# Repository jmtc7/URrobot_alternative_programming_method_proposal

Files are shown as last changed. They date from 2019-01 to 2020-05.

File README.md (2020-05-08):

# Alternative programming method for UR robotic arms
This project's objective is not to create a real full-operative alternative to the current programming methods for industrial robots but to propose an idea developing a Proof of Concept to show that this approach could have potential.

The project has 2 main parts:
* **3D-printable case** to contain and protect the Raspberry Pi, a camera, a distance sensor and a fan. It also makes it possible to attach the whole system to the UR robot wirst.
* **Python scripts** to program the robot and make it able to replay the teached movements. The robot has to be running its own (simple) program to move according the Modbus TCP-received messages.

Demos of the target segmentation (color and shape filtered) and of the final results (target tracking and following and trajectory reproduction) are available in the following **YouTube videos**:

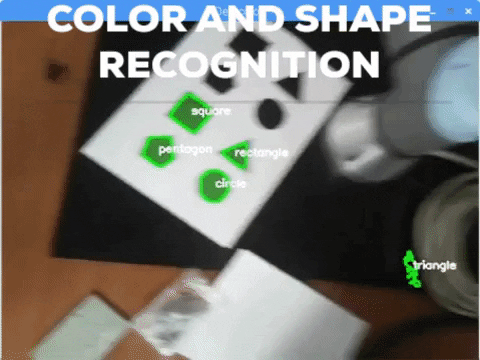
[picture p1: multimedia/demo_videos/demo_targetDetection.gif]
Target segmentation demo (https://www.youtube.com/watch?v=7s4_1wDeRGM&list=PLBYQePjTMEGEnVe6FjThMmySTzwtxLX1B&index=1)


Results demo (https://www.youtube.com/watch?v=rEhbCNIjvR4&list=PLBYQePjTMEGEnVe6FjThMmySTzwtxLX1B&index=2)

NOTE: This project was developed during my internship at [CFZ Cobots](https://cfzcobots.com/), in Elche (Spain), and submitted in a [competition](https://cfzcobots.com/i-concurso-cfz-de-aplicaciones-roboticas/) of applications designed for/with Universal Robots robotic arms.

## Documentation and usage
### Documentation
An exhaustive documentation of all the project can be found in the [project report](https://github.com/jmtc7/URrobot_alternative_programming_method_proposal/blob/master/documentation/report.pdf). A shorter version of it is in the [project presentation](https://github.com/jmtc7/URrobot_alternative_programming_method_proposal/blob/master/documentation/presentation.pdf). Even both of them are in Spanish, the next README sections are an overview of the project in English.

### Usage
In order to use this project, an Universal Robots robotic arm is needed, as well as a tool similar to the one proposed (with a camera and a distance sensor connected to a Raspberry Pi. The robot must be executing the [proposed robot program](https://github.com/jmtc7/URrobot_alternative_programming_method_proposal/tree/master/source_code/ur_program). Note that it is advisable to lower the robot velocity from the command pallete to be able to do a first test run safely. The tool must be connected to the robot so that it can write in its registers via Modbus TCP. Finally, a target will be needed, which consists in a green triangle that can be sticked in the tool which have to be followed.

Once having everything setted up as explained, the *programar.py* script should be executed in the tool. It will make the robot follow the target and store the corrections in a file named *correcciones.txt*. Once the desired trajectory is finished, the execution of this script must be stopped. Next, the robot can be moved to the desired point where we want it to start the trajectory and execute the *reproducir.py* script in the tool, which will read the corrections file and make the robot perform the programmed movements relative to the chosen start position.

## 3D case
I started attaching just the Raspberry and a camera to the wirst of the robot using flanges and adhesive tape to make some initial test and trials. I then developed a really simple 3D printed mounting that made it possible a more solid (yet **provisional**) attach between the robot and the two devices mentioned before. This mounting was composed by this two plates:
<p align="center">
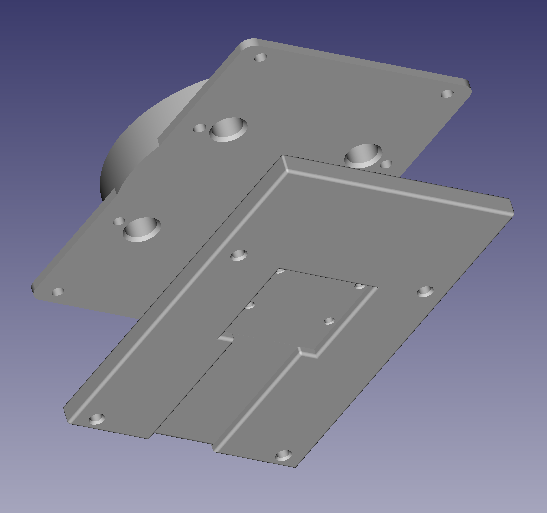
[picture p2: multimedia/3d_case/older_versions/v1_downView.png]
   
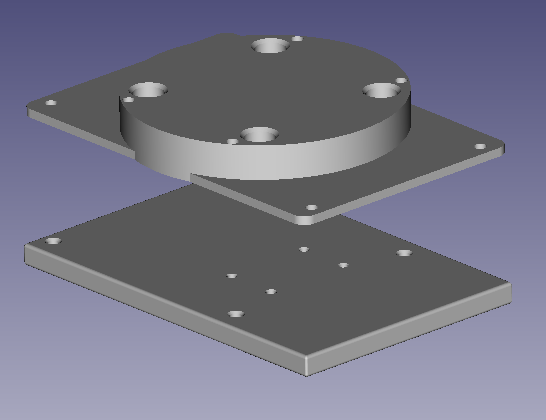
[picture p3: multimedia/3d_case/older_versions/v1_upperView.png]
  
</p>

Then, after advancing with the code, I started designing a **final version of a new case**. It will be adapted to the needs I met during the developement (such as including a distance sensor) and, obviously, will include general improvements such as a more aesthetic finish, more protection, ventilation, better and more solid coupling:
<p align="center">
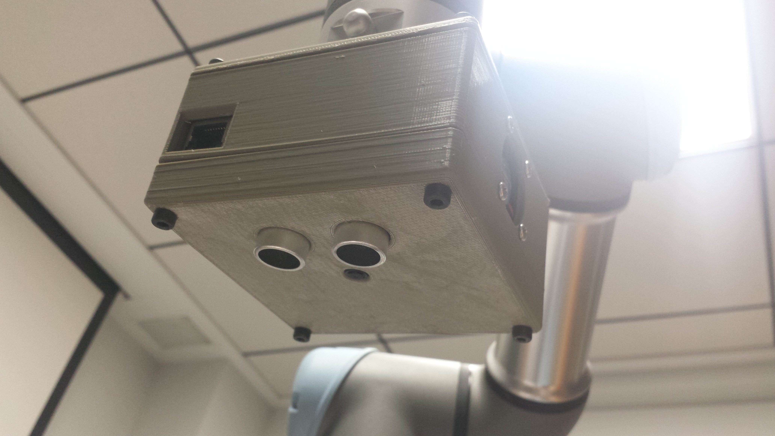
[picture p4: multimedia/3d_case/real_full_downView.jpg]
  
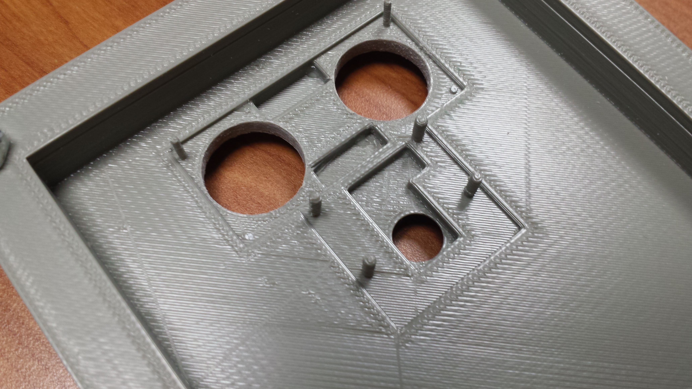
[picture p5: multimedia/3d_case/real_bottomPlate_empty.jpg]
  
</p>

<p align="center">
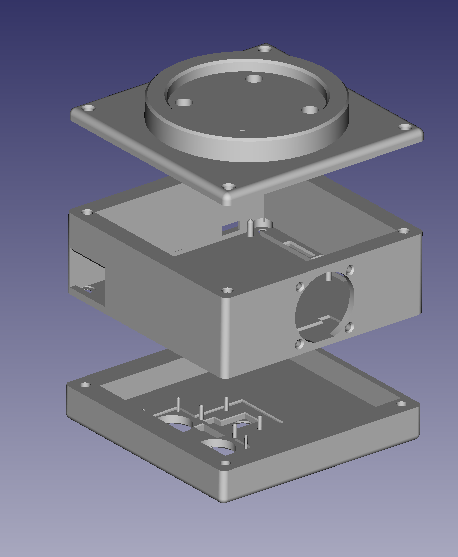
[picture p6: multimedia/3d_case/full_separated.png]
   
</p>

## Scripts
### Software in the tool
As mentioned in the introduction, in the tool, two Python scripts will be executed in the Raspberry Pi: *programar.py* and *reproducir.py*, both of them contained in the *source_code* folder.

* ***programar.py*** tracks the centroid of the biggest green triangle perceived by the camera. I convert to HSV, threshold and use the Ramer-Douglas-Peucker algorithm to classify shapes. Then, the neeeded cartesian corrections to center the centroid in the frame are calculated. Finally, they are sent to the robot (which will solve the inverse-kinematics to reach the new target) and written into a corrections file named *correcciones.txt* that will be used by the other script to reproduce the trajectory..

* ***reproducir.py***. This script does the same as *programar.py* but substituting the computer vision and corrections calculation for just reading a line of the corrections file *correcciones.txt*. The aquired data is then sent to the robot so that it will behave as it did during the programming phase.

### Software in the robot
Appart of these scripts runned on the tool, the robot has to be always processing the messages that it receive via Modbus TCP. This is done by the **7_4_pruebas_modbus** program, also contained in the *source_code* folder. This program will get the correction provided by the tool software using the robot's Modbus TCP registers and move the arm accordingly.

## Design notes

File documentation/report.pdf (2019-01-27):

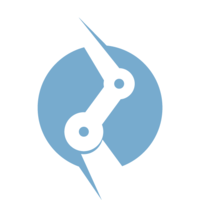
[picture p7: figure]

Prácticas extracurriculares en CFZ Cobots

Ingeniería Robótica, Universidad de Alicante

## Propuesta de un método alternativo de programación por guiado basado en visión artificial

Autor:
José Miguel Torres Cámara

Tutores:
Jorge Vergara Roa (empresa) Fernando Torres Medina (UA)

## Índice

1. Motivación, objetivos y estructura | 2
2. Resultados | 3
3. Recursos utilizados | 17
4. Otras versiones de la herramienta | 18
5. Otras opciones para el identificador | 22
6. Otras opciones para el procesado de imagen | 24
7. Otras opciones para las comunicaciones | 25
8. Análisis de resultados y conclusiones | 26
9. Trabajos futuros | 27
Referencias | 30

1

## 1. Motivación, objetivos y estructura

1.1. Programación por guiado

Actualmente se distinguen dos principales maneras de programar un robot: programación textual y programación por guiado. Mientras la textual consiste en escribir código de forma similar a como se hace en lenguajes de programación estándar, en la programación por guiado se mueve el robot hacia las posiciones que debe de alcanzar en cada momento, bien sea de forma discreta, es decir, moviendo al robot manualmente o desde la consola de programación a todos los puntos uno a uno e ir grabándolos independientemente o de forma contínua, en la que directamente se le coloca la herramienta que usará en la aplicación y se realiza la tarea que deberá reproducir el robot con la herramienta ya colocada en el extremo del mismo. Este último método es muy común en aplicaciones donde se requiere cierta habilidad o arte en la tarea, donde es complicado reproducir los movimientos que seguiría el humano artista mediante los otros métodos tradicionales. Algunas de estas tareas serían operaciones de pintura, soldadura, etc. Dada la versatilidad que supone este método así como su gran cantidad de aplicaciones y facilidad de programación de cara al usuario, durante el proyecto me centraré en él.
A pesar de todas las ventajas que supone este tipo de programación por guiado, también conlleva imprecisión en los movimientos (ya que lo mueve un humano) así como cierta incomodidad ya que el artista no estará ejecutando la tarea con su herramienta al aire, si no que tiene que arrastrar el robot tirando de ella, lo que puede suponer limitaciones espaciales así como un evidente esfuerzo extra, desenvocando en que sea prácticamente imposible realizar la tarea igual que si la herramienta no estuviese unida al robot.
A causa de esto, pensé en formas de mejorar el resultado que proporcionaba este tipo de programación tratando de evitar costes excesivos y manteniendo su sencillez de uso de cara al usuario, llegando así a la conclusión de que las opciones con más posibilidades era lograr que el robot pudiese almacenar las posiciones a seguir mientras el usuario realiza la tarea con la herramienta totalmente desacoplada del robot. De esta forma se reducirían parcialmente todos los contras comentados en el párrafo anterior.
1.2. Objetivos generales

Como principal objetivo tengo que, mis prácticas sirvan como un inicio de proyecto real, ya que en un mes no puede desarrollarse una alternativa de programación realmente práctica por lo que el objetivo, evidentemente, no es lograr una alternativa real a los métodos de programaciones actuales.
Con el objetivo de desarrollar este primer paso hacia un nuevo método de programación, pretendo desarrollar un prototipo mínimo que demuestre que es posible implementarlo, que permita descubrir posibles mejoras y que cumpla con algunas de las características que considero más importantes para este propósito, las cuales son:

2

Robustez: El prototipo debe de comportarse de forma similar en la mayor parte de los ambientes donde se ponga a prueba, tanto en un entorno controlado de laboratorio como en las muchas condiciones que puede suponer cualquier entorno industrial, ya que este último será su verdadero campo de aplicación

Efectividad: Debo lograr un seguimiento lo más cercano a la realidad que sea posible ya que, de no ser así, no tendría sentido utilizar esta propuesta. Con ese propósito, los movimientos del robot deberán ser todo lo suaves y naturales que se pueda, dando por sentado que se debe seguir la trayectoria del identificador fielmente. Otro punto importante es la velocidad con la que el robot puede seguir al objetivo sin perderlo, ya sea porque no pueda frenar de lo rápido que va o porque el objetivo vaya demasiado rápido

Sencillez: Como mencioné anteriormente, una de las principales ventajas de la programación por guiado es su carácter user-friendly, cosa que me gustaría conservar e incluso mejorar con esta aplicación. Quiero que el usuario final sólo tenga que montar el dispositivo en el robot e iniciar la ejecución del programa del robot

Comodidad: Trataré de hacer un dispositivo embebido, lo más pequeño y manejable que me sea posible

1.3. Estructura del informe

Con el propósito de lograr la mayor claridad posible en este informe, comenzaré explicando hasta donde llegué en el proyecto así como los recursos software y hardware en los que me basé para después seguir comentando otras opciones que contemplé durante su desarrollo así como algunas de las pruebas que hice para cada una de las partes del mismo. Luego analizaré los resultados y seguiré mencionando algunos de los trabajos futuros que podrían realizarse para seguir avanzando. Por último, acabaré con las conclusiones que saqué tras realizar todo el proyecto.

## 2. Resultados

Tras finalizar el periodo de prácticas logré un prototipo mínimamente funcional que era capaz de hacer que el robot siguiese al identificador (un triángulo verde), almacenar los movimientos que se hacen relativos a su posición inicial y luego repetirlos desde cualquier posición desde la que se parta (a no ser que ésta provoque la existencia de singularidades, colisiones o salidas del espacio de trabajo en algún momento de la trayectoria, es decir, limitaciones propias del robot). Todo esto lo posibilita la existencia de cuatro partes principales: una herramienta para el robot que controlada por una

3

Raspberry Pi, un programa del robot y dos programas en Python ejecutados en la Raspberry. Cada una de estas cuatro partes es la mejor versión que he podido crear de las mismas y, a continuación, paso a explicar cada una de esas versiones definitivas.

2.1. Herramienta desarrollada

Como he mencionado, he desarrollado una herramienta que puede acoplarse al extremo de cualquier modelo de los brazos robots de Universal Robots. Esta herramienta cuenta de tres partes:

Placa superior: Permite anclar la herramienta a la brida de herramienta de los brazos robóticos UR

Placa intermedia: Contiene el controlador, es decir, la Raspberry Pi (en concreto una 3B), que es la que se encarga de procesar la información captada por los sistemas de percepción y corregir la pose del robot. En esta parte de la herramienta también hay alojado un pequeño ventilador para refrigerar el sistema ya que, al estar todo encapsulado, se acumula bastante calor. También incorpora un divisor de tensión que adapta la señal que proporciona el sensor de distancia (un HC-SR04, basado en tiempo de vuelo de ultrasonidos). Evidentemente, esta placa cuenta con accesos desde el exterior al ventilador, al puerto ethernet y al microUSB de alimentación

Placa inferior: Esta última capa contiene tanto el módulo de cámara de la Raspberry (concretamente la revisión 2 del mismo) como el HC-SR04. La existencia de esta placa permite esconder tanto los cables como las PCBs del exterior, dejando únicamente visible las partes estrictamente esenciales. De este modo, logro una mayor protección para el sistema así como un acabado mucho más estético

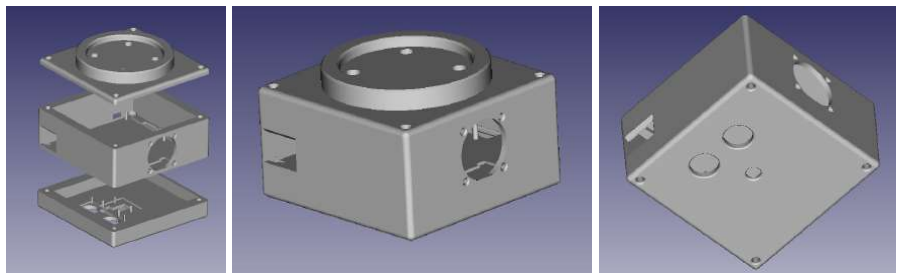
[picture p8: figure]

(a) Desglose de placas | (b) Vista superior | (c) Vista inferior

Figura 1: Diseño de la versión definitiva del soporte/herramienta

4

2.2. Script de programación (en Python) para la Raspberry

Este programa es el responsable de configurar la Raspberry tal y como se precisa en cada ejecución del programa, leer datos de la cámara y del sensor de distancia y calcular las correcciones que deben hacerse en en las posiciones X e Y del extremo del robot para reducir el error y enviárselas al robot para que se mueva, siguiendo al triángulo verde utilizado como marcador. También almacena estas correcciones en un archivo para su posterior lectura y reproducción de la tarea.

2.2.1. Dependencias y configuraciones previas

Existe una gran cantidad de recursos software que la comunidad ha creado y que facilitan enormemente el desarrollo de innumerables scripts que utilizan alguna de esas funcionalidades. Con tal de aprovechar esas bibliotecas, he utilizado algunas de ellas, como son:

time: Para contar el tiempo (función time()) que pasa entre que se emite la señal con el sensor de distancia hasta cuando se recibe y para hacer pausas (función sleep()) en varias partes del código

cv2 (OpenCV): Para capturar frames del módulo de cámara así como para realizar todo el procesado de imagen

pymodbus.client.sync: Para escribir los cuatro registros Modbus del servidor que se ejecuta sobre el armario de control del robot. Utilizo esos cuatro registros para indicar las correcciones que deben hacerse en la posición del extremo del robot para que este siga estando sobre el triángulo verde

os.path: La necesito para utilizar la función isfile(), que me permite comprobar si en el directorio actual ya existe un archivo con correcciones almacenadas de otro proceso de programación previo. En caso de detectar que ya existe un archivo, se le comunica al usuario y se da la opción de abortar la ejecución o de continuar y sobreescribirlo

RPi.GPIO: Me permite utilizar los pines GPIO (General Purpose Input/Output) para tomar lecturas del sensor de distancia

Por lo referente a la secuencia de inicialización del programa, comienzo inicializando algunas constantes de configuración, como son la dirección IP del robot y el puerto donde este tiene abierto el servidor Modbus-TCP o como la distancia aproximada (en Z) entre el sensor de distancia y la cámara, que empíricamente determiné que rondaba los 6 milímetros. Otra constante de mucha importancia es la longitud que tendrá el filtro de media móvil (LONG FILTRO) que utilizo. Por defecto está establecida a 4. Elevarla supondrá más estabilidad y robustez pero menos velocidad y precisión. También se establece un intervalo (AREA LOW y AREA MAX) en el que debe estar el area del triángulo verde (identificador) percibido por la cámara. Por último, también se

5

permite configurar el tamaño de la ZONA TOLERANCIA. Esta constante es el número por el que se dividirá el tamaño del frame captado, creando un rectángulo en el centro del mismo con las dimensiones que resulten de esas divisiones. Cuando el centro del identificador esté en ese rectángulo, se considerará que el robot está sobre el triángulo a seguir, por lo que no se moverá. Esto quiere decir que disminuir el tamaño del rectángulo (es decir, aumentar el valor de esta constante) supondrá más precisión pero aumentarlo demasiado hará que el rectángulo sea muy pequeño, pudiendo hacer que no se logre posicionar el centro del identificador en el mismo, haciendo que el robot oscile en torno a la posición sobre la que debería mantenerse estático.
Tras definir algunas funciones auxiliares (que explico en la siguiente sub-sub-sección del informe), continúo con otras inicializaciones que NO deben ser modificadas. La primera de estas es la del sistema de visión, es decir, lograr acceder al módulo de la cámara y leer un frame con éxito. En caso de no conseguirlo, se le indicará al usuario y el programa finalizará automáticamente. Se continúa con el sensor de distancia, inicialización para la que deshabilito las advertencias de posibles fallos que se hayan cometido en otros programas que usasen los GPIO y no los reconfigurasen debidamente. También indico que utilizaré la numeración de la placa y especifico los pines a los que se conectarán los pines Trig (disparador) y Echo (receptor) del sensor, además de configurarlos como salida y como entrada, respectivamente.
Tras configurar los sistemas de percepción, continúo con las comunicaciones, es decir, abriendo el socket que me permite escribir los registros del servidor Modbus del robot. En caso de que sucediese algún error durante la conexión, se informará al usuario y se finalizará la ejecución de forma automática. Tras esto, abro el archivo de escritura, que estará en el mismo directorio que el programa y se llamará çorrecciones.txt”. Comienzo comprobando si ya existe un archivo con ese nombre en el directorio. En caso positivo se informará al usuario y se dará la opción tanto de abortar la ejecución como de continuarla (y sobreescribir el archivo).
Continúo las inicializaciones declarando algunas variables para el procesado de imagen, tales como el intervalo en HSV que se considerará verde, que determiné empíricamente por mi cuenta. También leo las dimensiones de los frames y asigno valores iniciales a algunas variables por cuestiones de optimización de código como evitar declaraciones y destrucciones iterativas que consuman tiempo y coste computacional innecesariamente. Por último, adapto algunas variables del algoritmo al entorno según la distancia que haya entre la superfície más próxima a la cámara y la cámara, ya que de esta magnitud dependerán el tamaño de las correcciones que se le ordenen al robot. Tras inicializar algunas variables por los mismos motivos que en la inicialización del procesado de imagen, tomo varias medidas del sensor de distancia (el doble de elementos contenidos en el filtro de media móvil), de las cuales hago la media, considerando al resultado de la misma la distancia cámara-superficie anteriormente mencionada tras añadirle la corrección de la constante de configuración. Por último, calculo los desplazamientos máximos que debería hacer el robot en X e Y para seguir al identificador. Estas correcciones será la distancia real que hay entre lo que en el frame aparece en el centro del mismo y en la mitad de los bordes derecho o izquierdo (corrección en X) y en la mitad de los bordes

6

superior o inferior (corrección en Y). La relación entre la altura y esas distancias las obtuve con cálculos trigonométricos sencillos que no incluí en el códiogo por aligerarlo. Estos cálculos utilizan los ángulos de visión de la cámara y la ley del seno.
Sabiendo que, según [1], el ángulo de visión de la cámara es de 62.2◦ en X y de 48.8◦ en Y, es posible calcular las correcciones de la siguiente manera:

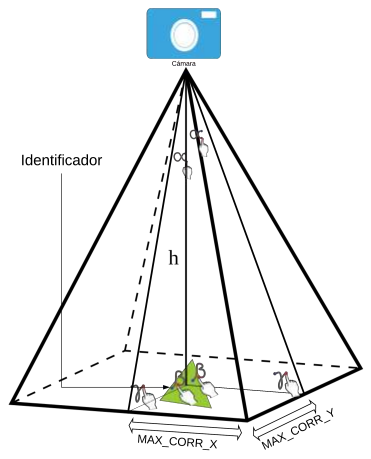
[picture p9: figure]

Figura 2: Representación del área de visión de la cámara

Cálculo de la corrección máxima en X
Angulo de visión en X = 62.2 ´ | ◦
α =

62,2
2 = 31.1◦
h = lectura del sensor de distancia β = 90◦
γ = 180 − 90 − 31,1 = 180 − 121,1 = 58.9◦
Teorema del seno:

CORR MAX X
sen(α) | = h sen(γ)

CORR MAX X =h · sen(α)
sen(γ)

=

=

h · sen(31,1)
sen(58,9) = 0.6032386 · h

Cálculo de la corrección máxima en Y
Angulo de visión en Y = 48.8 ´ | ◦
α =

48,8
2 = 24.4◦
h = lectura del sensor de distancia β = 90◦
γ = 180 − 90 − 24,4 = 180 − 114,4 = 65.6◦
Teorema del seno:

CORR MAX Y
sen(α) | = h sen(γ)

CORR MAX Y =h · sen(α)
sen(γ)

=

=

h · sen(24,4)
sen(65,6) = 0.4507694 · h

7

2.2.2. Funciones auxiliares

En pos de un código lo más limpio y claro posible, he definido varias funciones auxiliares que me permiten evitar la inclusión en el cuerpo principal del programa de código que dificultarían su lectura. Estas funciones son:

media movil(): Me permite añadir robustez y estabilidad a las lecturas de posiciones de la característica en el frame actual. Recibe como argumentos de entrada dos vectores que almacenan el historial de las últimas posiciones (en píxeles) del identificador. Uno de los historiales es sólo de las coordenadas X y, el otro, de las Y. Los historiales albergarán tantas medidas como indique la constante de configuración LONG FILTRO. Cuanto más alto sea su valor, más robusto será el proceso a lecturas erróneas (ruido puntual) pero se seguirá a la característica con menor precisión y velocidad. Un valor aconsejable es 4. A partir de los dos historiales, calcula la media y devuelve los resultados

detectarTriangulo(): Evalúa si un contorno es o no un triángulo. Basada en el algoritmo de Ramer-Douglas-Peucker, que simplifica un segmento curvo aproximando varios segmentos lineales. Esto permite saber cuántos vértices principales se tienen en un contorno determinado. El contorno a analizar es su único argumento de entrada. Este contorno estará formado por una serie de puntos obtenidos tras el procesado de la imagen. Simplemente realizo la aproximación por segmentos lineales y, en caso de haberse aproximado con tres segmentos, confirmo que la forma es un triángulo devolviendo un valor True. En caso de que la aproximación no resultase en tres contornos, se devuelve False

medirDistancia(): Hace uso de los pines GPIO para medir la distancia desde el sensor de distancia (y de la cámara) hasta el objeto más cercano (superfície donde esté el identificador). Pone a nivel bajo el pin que ordena que se emitan señales desde el sensor y se hace una pequeña pausa (2 microsegundos) para que de tiempo a que se haya apagado. Después, se enciende dicho pin, ordenando una emisión de ultrasonidos para continuar con otra pausa (de 10 µs) para asegurar la emisión antes de volverlo a apagar. Después se comienza a contar tiempo cuando se recibe un valor alto a través del pin que indica si el receptor recibe o no. La cuenta se detiene cuando para de recibir. Por último, se calcula el tiempo transcurrido entre estos dos eventos y se utiliza ese dato para calcular la distancia hasta el objeto más próximo en metros. El resultado de esta conversión será el valor que devuelva la función

2.2.3. Bucle principal: Procesado de imagen

El objetivo del procesado de imagen que realiza mi programa es obtener el centroide del contorno (sucesión de puntos) del triángulo verde más grande que aparezca en el frame. Con este propósito, desarrollé un procesado de imágen divisible en dos partes: discriminación por color y por forma y tamaño.

8

La discriminación por color fue por la que empecé, detectando el verde, ya que tras numerosas pruebas, determiné que era el color que se reconocía con más robustez antes cambios de iluminación y para áreas de distintos tamaños y formas. Para esta parte, comienzo pasando de RGB a HSV, ya que en este espacio de color se separa el tono de la luminosidad, logrando muchísima más robustez frente a variaciones en la luminosidad. Además, dada su distribución cilíndrica de los colores, es más sencillo establecer un único intervalo en el que se localizan los colores deseados. Esta transformación la realizo con la función cvtColor() de OpenCV[3].
Una vez convertida la imagen a HSV, creo una imagen binaria en la que los píxeles cuyo valor entren en el intervalo establecido en las constantes de configuración aparecerán en blano y, el resto, en negro. La ubralización la permite el método inRange().

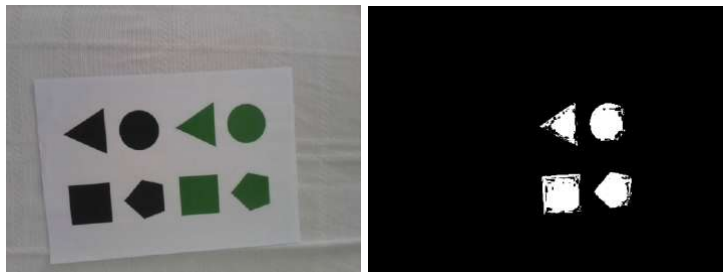
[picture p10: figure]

(a) Frame original | (b) Frame binarizado

Figura 3: Umbralización por color

Sobre esta imagen binaria, con findContours(), también de OpenCV[3], obtengo todos los contornos que envuelven a las figuras que en ella aparecen, que incluirán tanto las áreas verdes que aparezcan como los ruidos que figuren en la imagen por cualquier causa.
Una vez obtenidos todos los contornos, paso a discriminarlos por tamaño y forma. Se recorre el vector de contornos obtenido (la variable cnt) para evaluar el área que encierra cada uno de ellos, siendo esta la primera ”barrera”que deben pasar para ser considerados el identificador. Si el contorno que se esté evaluando es el mayor hasta el momento, se comprueba si además es un triángulo (con mi función detectarTriangulo()). En caso de cumplir ambas condiciones, se almacena tanto el contorno como el área que encierra para poder disponer de los mismos después.

9

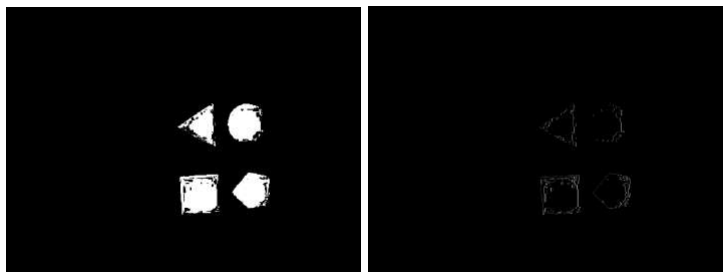
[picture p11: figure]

(a) Frame binarizado | (b) Contornos extraidos

Figura 4: Extracción de contornos

Tras analizar todos los contornos detectados, se dispondrá del que corresponda al triángulo verde más grande de la imagen, habiendo discriminado tanto triángulos de otros colores como ruidos pequeños, posibles reflejos, otras formas verdes, etc.

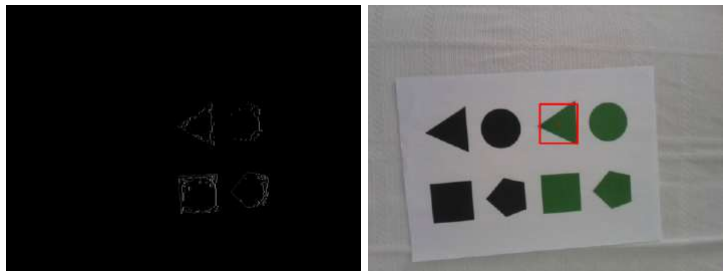
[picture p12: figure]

(a) Contornos extraidos | (b) Detección definitiva

Figura 5: Discriminación por forma

El hecho de haber escogido al triángulo como forma discriminadora vino dado tras un análisis con varias formas (triángulos, cuadrados, rectángulos, pentágonos y círculos) de varios colores y tamaños. Traté de detectarlos desde distintas distancias y orientaciones y el que se comportaba mejor casi siempre era el triángulo. Las figuras con más aristas se confundían cuando las enfocaba con inclinaciones elevadas o desde distancias relativamente largas.

10

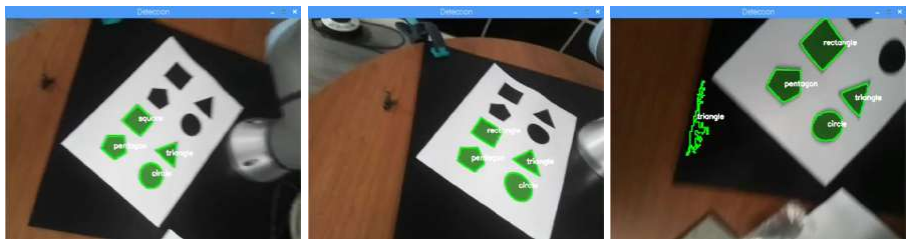
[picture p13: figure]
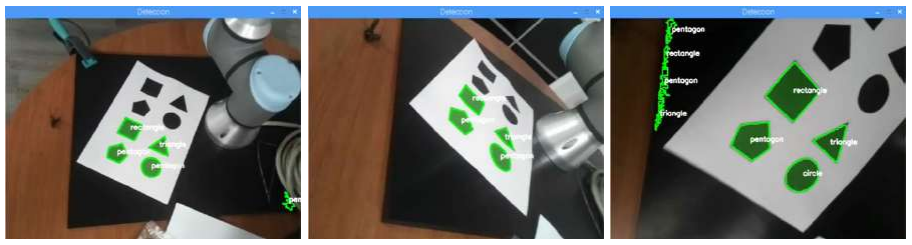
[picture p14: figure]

Figura 6: Detección y clasificación de varias formas con varios ángulos y tamaños

Tal y como se aprecia en las imágenes (extraídas de un vídeo en el que detectaba y clasificaba formas on-line), el círculo es el que más se confunde, normalmente con figuras de muchos lados (considero que es un círculo cuando se detectan 6 o más vértices). Sin embargo, en ningún momento se confunde al círculo con un triángulo. Dado que, como he mencionado, las imágenes son de un vídeo, algunos frames eran muy borrosos, por lo que no he incluido uno de ellos en el que el pentágono se confunde con un círculo. Estos dos hechos dejan como mejores opciones a los cuadrados/rectángulos y a los triángulos. Dado que, como he mencionado, el círculo nunca se ha confundido con un triángulo pero sí con un cuadrado, opté por descartar a los cuadriláteros, ya que podría darse el caso en el que hubiese un círculo verde en la escena y este deba ser discriminado, cosa que se logra utilizando triángulos en lugar de cuadrados o rectángulos. También se observa que los ruidos son formas pequeñas, por lo que se discriminarán, así como que otras formas de otros colores, como negras, no son tenidas en cuenta.
La última discriminación consiste en comprobar si el área del contorno resultante está en el intervalo definido en las constantes de configuración(AREA TOP y AREA LOW). Esto permite detectar cuándo ningún contorno cumplía con todos los requisitos (area max seguirá siendo 0, estando por debajo de AREA LOW) así como detectar posibles errores en los que se considere un contorno exageradamente grande. Si el contorno está en el intervalo definido, calculo su centroide ([cx, cy]) utilizando los momentos del mismo.
En caso de que no haya ningún contorno triangular que encierre un área de un tamaño aceptable, se notifica y se centra toda la potencia de procesado en encontrarlo, haciendo un continúe, obligando a reiniciar el bucle (que vuelve a

11 tomar otro frame y a procesarlo) en lugar de seguir con el cálculo y el procesado de las correcciones.

2.2.4. Bucle principal: Cálculo de correcciones

Tras el procesado, he obtenido los valores de cx y de cy, por lo que ya se puede continuar con el siguiente paso: transformar la posición del identificador en la imagen en correcciones para la posición del extremo del robot.
Antes de calcular nada, se guardan las coordenadas en píxeles del identificador en los historiales historial x e historial y y se comprueba su longitud. En caso de ser menor que la configurada en la constante LONG FILTRO, se vuelve a iniciar todo el procesado de imagen para tomar otra medida de la posición del identificador, de forma que hasta no haber llenado un ”buffer”del filtro, no se inicia el funcionamiento normal del bucle.
En caso de que se disponga de suficientes medidas, se elimina la más antigua (el elemento 0 de los historiales) y se calcula la media, considerando el resultado de la misma la posición actual del identificador, siendo esta la que se utiliza para calcular las correcciones.
Las correcciones en cada eje (X e Y) se calcularán sólo si en ese eje el identificador está fuera de la zona de tolerancia (rectángulo verde de la figura 6), es decir, fuera del rectángulo que se establece en el centro del frame en el que se considera que, si el centro del identificador (punto rojo de la figura 6) está dentro, el robot está sobre el mismo, caso en el que a la corrección en ese eje tomará un valor de
0. El uso de esta zona viene dado porque, si no la utilizaba o si era demasiado pequeña, el robot oscilaba sobre la posición objetivo. En la siguiente imagen es una catorceava parte del temaño total del frame:

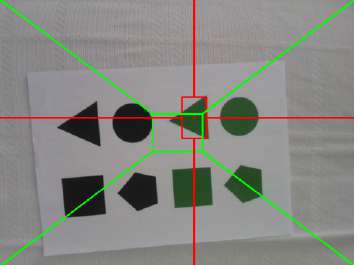
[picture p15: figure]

Figura 7: Zona de tolerancia

En caso de ser necesaria corrección en alguno de los ejes, calculo y normalizo (entre 0 y 1) el error de la posición del centro del identificador, asumiendo como posición deseada el píxel central del frame. A ese valor entre 0 y 1 lo multiplico por la corrección máxima calculada en el eje que corresponda (DESPLAZAMIEN-TO MAX X para el eje X y DESPLAZAMIENTO MAX Y para el eje Y), obteniendo

12 el desplazamiento que el robot deberá hacer para posicionar la cámara (que gracias al diseño de mi herramienta, tiene el eje Z alineado con la muñeca del robot) sobre el identificador.

2.2.5. Bucle principal: Procesado de correcciones

Tras haber calculado las correcciones a hacer (correccionX y correccionY ), paso a procesarlas. Este procesado consiste únicamente en comunicárselas al robot por Modbus-TCP y en anotarlas en el archivo correcciones.txt.
Para comunicarle los resultados al robot utilizo cuatro registros Modbus. El uso de cuatro registros en lugar de dos es porque estos sólo pueden contener valores positivos, así que escribo las correcciones a hacer en X y en Y en los registros 128 y 129 y sus signos en los 130 y 131, escribiendo ”1”si es positivo y ”0”si es negativo. Por lo referente a los registros 128 y 129, escribo el valor absoluto del resultado de dividir las correcciones multiplicadas por 1000 y divididas por 2. Las divido entre 2 para evitar sobreoscilación durante el seguimiento, sacrificando velocidad. El hecho de multiplicar las correcciones por 1000 es debido a que los registros sólo pueden contener números enteros, por lo que lo escribo en milímetros en lugar de metros cosa que luego, en el programa del robot, tengo en cuenta.
Por último, también escribo las correcciones en el archivo. Para no perder tiempo, no vuelvo a hacer las operaciones de multiplicar por 1000 y dividir entre 2, cosa que SÍ que hago en el programa de reproducción, ya que este conlleva una carga computacional mucho menor.
2.2.6. Proceso de finalización

Con tal de lograr una finalización lo más limpia posible, he tratado de contemplar todas las posibles excepciones, tales como errores en las diferentes inicializaciones, peticiones del usuario o una interrupción de teclado (Ctrl + C). Si ocurre cualquiera de estas cosas, libero la cámara (liberando el archivo de captura así como la memoria reservada para su uso), cierro el socket que utilizo para Modbus/TCP (sólo si se ha conseguido abrir durante las inicializaciones), libero el archivo de escritura y reseteo los GPIO utilizados durante el programa (11 y 13 según la numeración de la placa para el sensor de distancia).

13

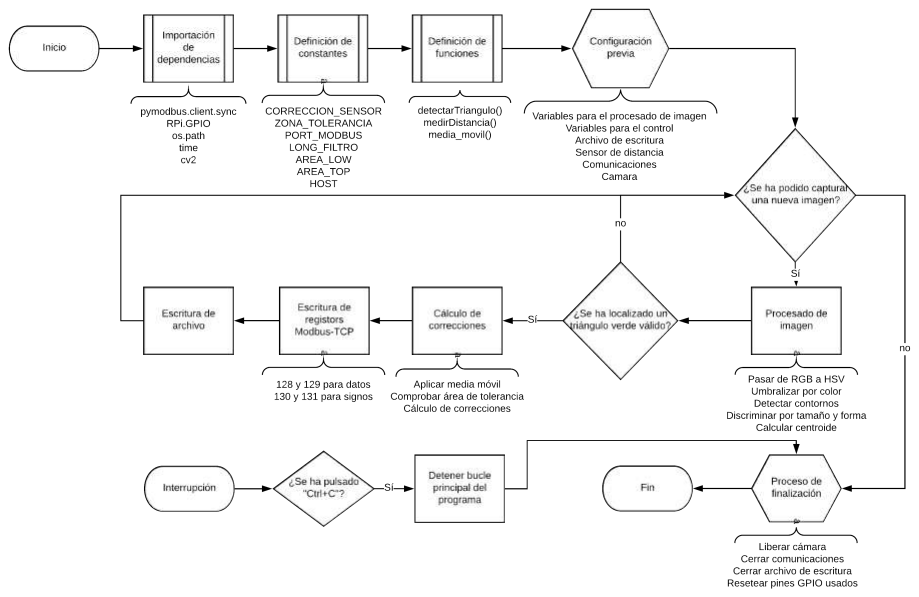
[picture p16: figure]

Figura 8: Diagrama de flujo de programar.py

2.3. Script de reproducción (en Python) para la Raspberry

Este programa se ejecutará una vez se haya programado al robot mediante una ejecución completa, exitosa y sin errores del anterior programa (caso normal), de forma que se haya creado el archivo. Este script permite que se reproduzcan los movimientos realizados durante la programación sin perder el tiempo que se perdió con el procesado de imagen y cálculo de correcciones, además de consumir menos recursos, ya que exige mucha menos memoria y potencia de cálculo para su ejecución.
Dado este método de reproducción, no hace falta cargar un programa distinto en el robot, ya que basa las comunicaciones en el mismo funcionamiento del programa anterior, escribiendo los mismos 4 registros Modbus.
2.3.1. Dependencias y configuraciones previas

Al igual que en el caso del programa anterior, utilizo algunas librerías ya desarrolladas por la comunidad. Aunque menos que en el caso anterior, todas también se usan en el

14 otro programa. Las dependencias que importo son os, time y pymodbus.Client.sync. Les doy los mismos usos que en el script para programar al robot.
Además de incluir estas dependencias, antes de iniciar el funcionamiento normal del programa, realizo una serie de configuraciones previas, como son la declaración de las constantes de configuración, como la IP del robot (HOST), el puerto donde el mismo tiene el servidor Modbus (PORT) y el tiempo que se deja entre cada escritura de registros (DELAY ITERACIONES). Este tiempo está configurado a 0.048496 s porque es el tiempo medio que se tardaba en una iteración completa del bucle del script de programación. De este modo, el comportamiento durante al reproducción será lo más similar posible al que tuvo lugar durante la programación.
A continuación, al igual que hacía en el otro programa, abro el archivo de lectura donde se almacenaron las correcciones realizadas durante la programación y abro un socket para comunicarme por Modbus-TCP con el robot. Tras este último paso, escribo un 0 en los registros de correcciones del robot para que, en caso de que por cualquier motivo, tuviesen otro valor, el robot no se moviese cuando no debe hacerlo. También tengo en cuenta posibles errores, como que el archivo no exista o que haya algún fallo durante la conexión con el servidor, en cuyo caso, se le comunicaría al usuario y se abortaría la ejecución del programa.
2.3.2. Bucle principal

Este programa únicamente lee las correcciones almacenadas en el archivo, las transforma de tipo y las escribe en los registros Modbus por Modbus-TCP que usaba la otra aplicación, permitiendo que el robot las lea y corrija su posición. Entre escritura y escritura se realiza un pequeño delay que simula el tiempo que se tardó en todo el procesado de imagen y cálculo de correcciones en el otro programa, reproduciendo todo lo fielmente posible los movimientos realizados.
El usuario podrá regular la velocidad de reproducción de movimientos desde la barra de velocidad de la consola de programación y, como opción excepcional, reduciendo el tiempo de delay, aunque la diferencia será mínima.
2.3.3. Proceso de finalización

Para finalizar este programa, repito una parte de la secuencia de finalización del otro programa. Concretamente, la de cerrar el socket y liberar el fichero desde el que se leen las correcciones almacenadas.

15

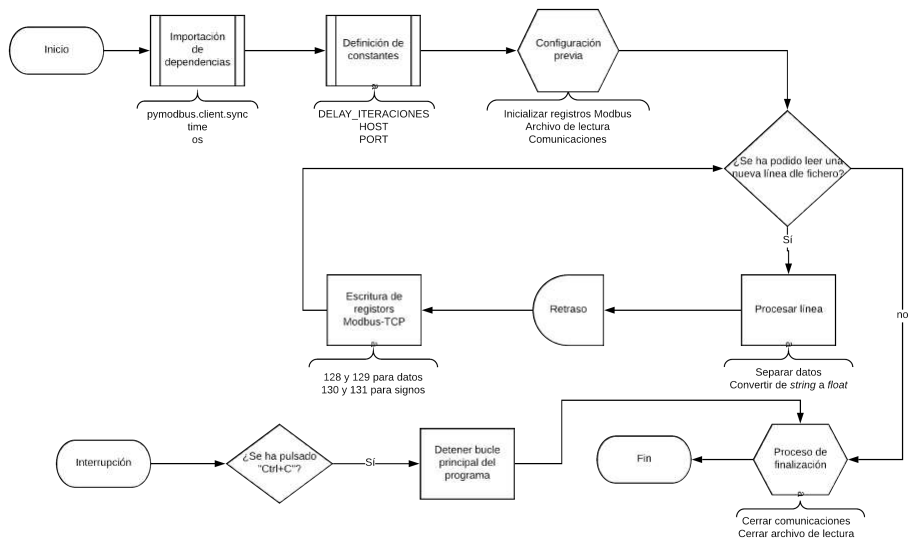
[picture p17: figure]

Figura 9: Diagrama de flujo de reproducir.py

2.4. Programa del robot

Para llevar a cabo las correcciones calculadas por la Raspberry, desarrollé un pequeño programa para el robot que procesaba los datos enviados a través de Modbus-TCP al robot y hacía uso de algunas de las funciones que los UR ponen a disposición de los desarrolladores, como get actual tcp pose(), read port register(), pose trans() o MoveL(). Este programa es tremendamente sencillo pero permitía ahorrarle a la Raspberry una considerable carga computacional y simplificar muchísimo los códigos, cosa que era uno de mis principales objetivos, ya que el cuello de botella reside ahí, ya que se tarda sobre 50ms en llevar a cabo una iteración del bucle de control mientras que el robot es capaz de actuar recibiendo órdenes a 125Hz (una cada 8ms). Es debido a este ahorro temporal por lo que decidí utilizar este programa, ya que también disponía de otras versiones en las que no era necesario ejecutar absolutamente nada desde el robot. Además, al obligar a que cada programa se ejecute con una configuración de instalación concreta, permite reducir la posibilidad de que el usuario final tenga problemas que le puedan resultar complicados de solucionar, como algunos relacionados con la configuración de la red local RPi - robot.
El programa simplemente lee los registros Modbus de correcciones escritos por el programa de la Raspberry y, en caso de ser distintos de 0 (para no perder tiempo

16 inútilmente), les asigna el signo que les corresponda leyendo el otro par de registros Modbus, transforma la posición actual del TCP en la deseada y ordena un movimiento lineal hasta la misma, reduciendo el error en la medida que la Raspberry lo ordene.

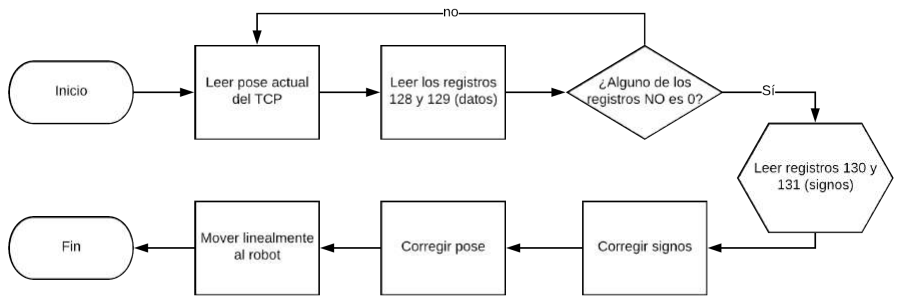
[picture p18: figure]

Figura 10: Diagrama de flujo del programa del robot

## 3. Recursos utilizados

3.1. Dispositivos involucrados

Como ya he mencionado, el elemento central de todas las pruebas que he realizado, ha sido una Raspberry Pi (modelo 3B concretamente). Este ordenador lo manejaba a través de una conexión VNC desde mi portátil. El otro factor constante en mis experimentos era un robot UR3 de la serie CB de Universal Robts.
Por otro lado, he ido utilizando varios accesorios para las pruebas, como la versión 2.1 de la cámara de la Raspberry, un módulo HC-SR04 para medir distancias, una IMU MPU6050 y, para algunas pruebas, un Arduino UNO.
3.2. Recursos software

Dejando de lado el Polyscope ejecutado sobre el Debian del UR3, he estado utilizando Raspbian corriendo sobre la RPi. Así mismo, para realizar pruebas de cada programa utilizaba Python y luego transcribía el código definitivo a C++, para poder compilarlo y obtener un binario que pudiese ejecutarse más rápido de lo que un script interpretado por el intérprete de Python podría. Sin embargo, dejé las versiones finales

17 en Python porque consideré que se alcanzaban velocidades aceptables, además de la inmensa diferencia a la hora de leer y depurar el código, siendo en el caso de Python mucho más sencillo.
Respecto a recursos más relacionados con mi aplicación y pruebas, he utilizado la librería Armadillo para C++ para implementar parte de los códigos con una carga matemática más compleja (como cálculo pseudoinversas, etc.). También usé OpenCV para llevar toda la parte de visión, tanto en C++ como en Python. Por lo referente a las comunicaciones, usé los paquetes socket y pymodbus en Python (para TCP y Modbus respectivamente) así como algunos otros de uso común como time, numpy, struct , os o RPI.GPIO.
Por otra parte, para testear las comunicaciones utilicé la versión 3 de socketTest, un programa que permitía a la máquina que lo ejecutase ser cliente o servidor TCP en la IP y puerto que se le configurase. Para Modbus hice uso de diagslave, que actúa como servidor. Ambos están disponibles tanto para Windows como para GNU/Linux.

## 4. Otras versiones de la herramienta

Para realizar pruebas era necesario tener la cámara en el extremo del robot de forma que la cámara viajase con el mismo, ahorrando el máximo de transformaciones entre sistemas de coordenadas o conversiones de desplazamientos innecesarias. En un inicio utilicé simplemente cinta adhesiva, aunque para las primeras pruebas fijé la Raspberry al robot con bridas y limité el uso de la cinta para sujetar la cámara al extremo del robot:

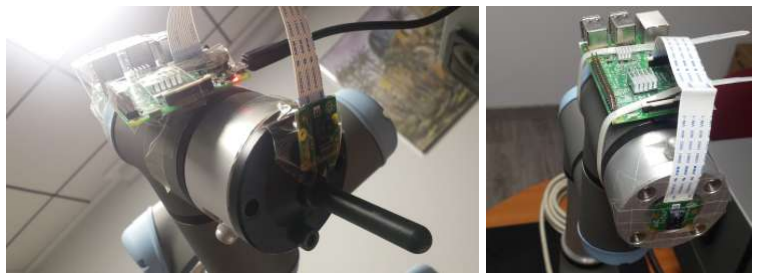
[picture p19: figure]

(a) Sujeción con cinta adhesiva | (b) Sujeción con bridas

Figura 11: Sujeciones provisionales

Sin embargo, como es evidente, esta no fue la sujeción final. Tras numerosos bocetos, diseñé varias posibles herramientas para el robot que permitiesen la máxima

18 limpieza y practicidad posibles. Para diseñar las piezas de las herramientas utilicé FreeCAD[6] y para las impresiones 3D, una RAISE 3D con ABS gris.

4.1. Primera versión de la herramienta

El principal problema que tenía es que, cuando fallaba el control, dadas las limitaciones físicas que suponía la longitud del cable de la cámara, muchas veces se desconectaba y en ocasiones me tocaba reinicar la Raspberry porque no la detectaba tras reconectarla, etc. Esto suponía una gran pérdida de tiempo además de ser intolerable para cualquier aplicación real. Por esto, decidí optar por un soporte que uniese la Raspberry y la cámara haciendo que ambos dispositivos se muevan con la tercera muñeca del robot.
Varios de mis diseños establecían el riesgo de que la Raspberry se chocase con alguno de los últimos eslabones con relativa facilidad ante movimientos inesperados del robot. Sin embargo, acabé optando por, a pesar de que el resultado sería más voluminoso, dejar paralelas tanto la Raspberry como la cámara al muñón del robot utilizando dos placas, una de las cuales iría enganchada al extremo del robot por encima y a la Raspberry y a la segunda placa por debajo. La cámara se atornilla por la parte inferior de la segunda placa.

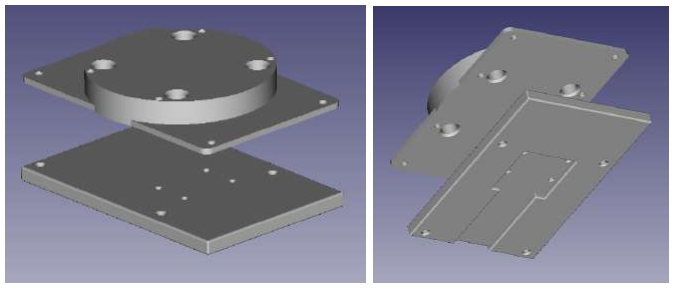
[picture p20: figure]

(a) Vista superior ideal | (b) Vista inferior ideal

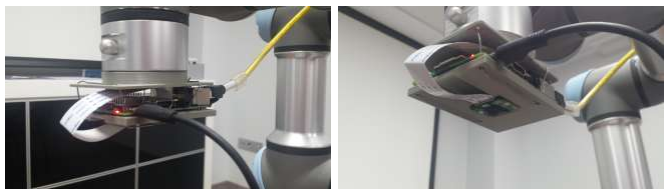
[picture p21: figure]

(c) Vista superior real | (d) Vista inferior real

Figura 12: Diseño de la primera versión del soporte/herramienta

En este soporte el principal problema que tuve fue encontrar los tornillos

19 y pilaretes necesarios como para que quedase bien anclado todo, ya que debían ser relativamente largos dada la magnitud de los agujeros, que estaba limitada por los anclajes de la Raspberry y de la cámara. Así mismo, el hardware quedaba bastante desprotegido y no es estético ver todos los cables y componentes al aire.

4.2. Segunda versión de la herramienta

En una segunda versión, a pesar de que la anterior era funcional, me enfoqué en hacer un soporte más estético, además de añadir ciertas mejoras, como la presencia de un hueco para un pequeño ventilador que refrigere el sistema y otro para añadir el sensor HC-SR04 para medir distancias. Además, todo quedaba completamente cubierto, pasando a mejorar los apartados estéticos y de protección respecto a la versión anterior.
Esta segunda versión sólo deja al descubierto las partes esenciales, tales como los agujeros para anclar la herramienta al robot, los agujeros para los tornillos que unen cada una de las tres placas y los agujeros para poder acceder al puerto ethernet, al microUSB de alimentación, al objetivo de la cámara y al emisor y el receptor del sensor de distancia.

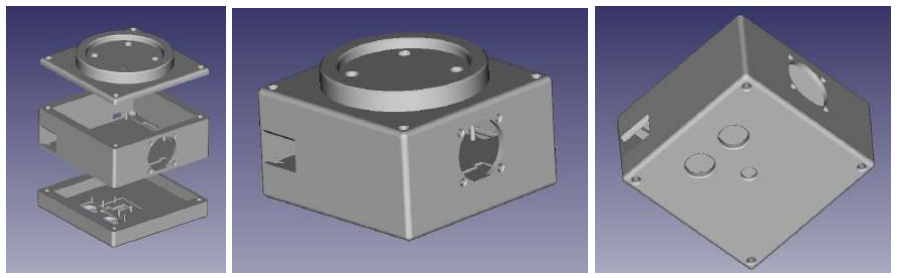
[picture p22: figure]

(a) Desglose de placas | (b) Vista superior ideal | (c) Vista inferior ideal

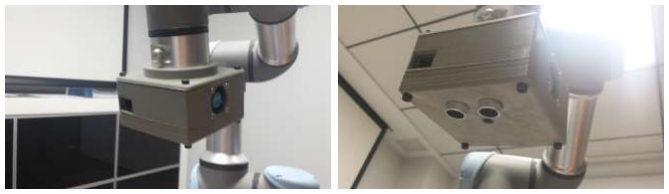
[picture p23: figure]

(d) Vista superior real | (e) Vista inferior real

Figura 13: Diseño de la segunda versión (y definitiva) del soporte/herramienta

La placa inferior tiene particular complejidad debido a los surcos que permiten colocar la cámara y el sensor de forma que queden bien sujetos aprovechando las

20 características físicas de los mismos. Todo esto se aprecia en más detalle en las siguientes imágenes:

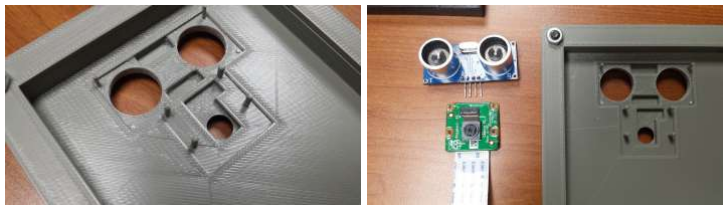
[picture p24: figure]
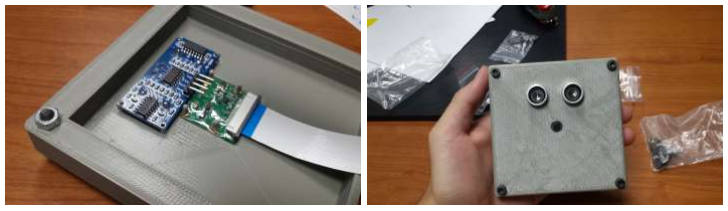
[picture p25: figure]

Figura 14: Vistas detallada de la placa inferior

A continuación muestro parte del proceso de diseño de esta herramienta, como el primer boceto a mano alzada sobre el papel y algunos recortes que realicé para pulir detalles y comprobar que las medidas eran las adecuadas:

21

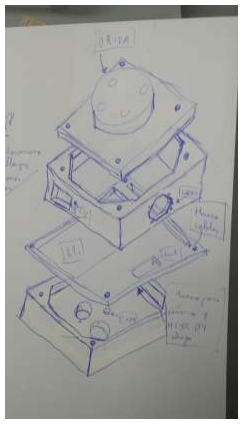
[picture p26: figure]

(a) Boceto inicial

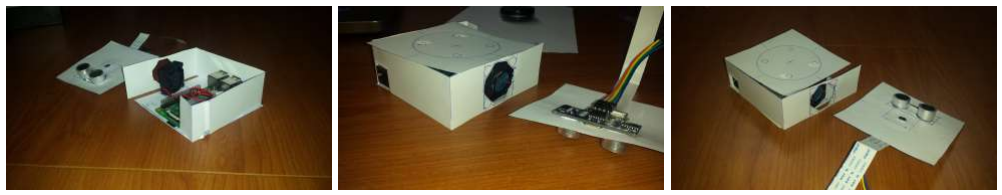
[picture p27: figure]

Figura 15: Boceto y construcciones en papel de la segunda versión

## 5. Otras opciones para el identificador

Enfocando el proyecto desde la opción del control visual, todas las opciones para detectar la herramienta que mejor resultado me dieron (midiendo la calidad según la velocidad y robustez con las que obtenía los resultados) se basaban en segmentación y, las finales, también en detección por formas (más robustez a cambios de iluminación, reflejos y ruido aunque con más carga computacional). Hasta que llegué al triángulo verde, realicé pruebas con varios patrones:

Cuatro puntos negros sobre fondo blanco (y puntos blancos sobre fondo negro). Logrando un alto contraste que favorecía la sencillez de la detección y permite una segmentación en intensidad RGB, disminuyendo bastante la carga computacional pero arriesgando la robustez, ya que pueden detectarse falsos positivos con gran facilidad en entornos no controlados

22

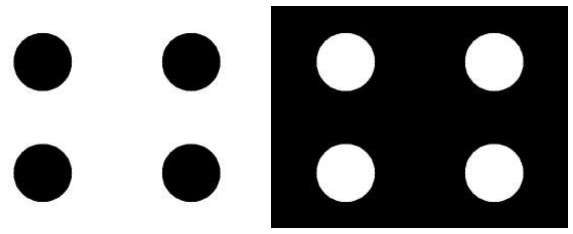
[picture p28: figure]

(a) Puntos negros en fondo blanco (b) Puntos blancos en fondo negro

Figura 16: Identificador con cuatro puntos de alto contraste

Cuatro puntos verdes. De este modo, a pesar de exigir segmentación multicanal en HSV para lograr una buena robustez, se logra una detección mucho mejor que en el caso anterior, ya que en un entorno industrial, normalmente, no habrán objetos de estos colores y, si los hubiese, bastaría con modificar los umbrales e imprimir un identificador de otro color

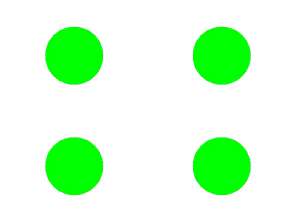
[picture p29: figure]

Figura 17: Identificador con cuatro puntos verdes

Cuatro puntos de un color distinto cada uno. De este modo consigo codificar todos los posibles estados de rotación en Z del identificador. También permite implementar métodos para incrementar muchísimo la robustez (a costa de consumo de recursos computacionales y tiempo). Por contra, supone cuatro segmentaciones y, por tanto, requiere de un procesado de imagen mucho más pesado, incluso optimizándolo todo lo posible

23

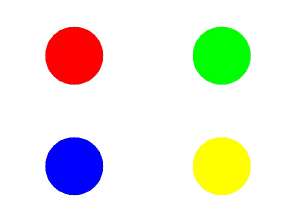
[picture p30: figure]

Figura 18: Identificador con cuatro puntos de cuatro colores

Un único punto amarillo. Así se reduce la aplicación a planos o superfícies con pocas variaciones, aunque también implica una gran disminución de la carga computacional exigida

Un triángulo verde. Tras realizar algunas pruebas, concluí que la detección de verde era más robusta a través del mismo procedimiento que la detección de amarillo. El utilizar un triángulo en lugar de un círculo vino dado por confusiones puntuales durante el seguimiento, en el que reflejos u otros elementos ocasionalmente hacían que el objetivo no estuviese en el identificador. Dada esta situación, decidí endurecer la localización del identificador utilizando el algoritmo de Ramer-Douglas-Peucker. Este algoritmo simplifica un contorno componiéndolo con varios segmentos lineales, lo que permite contar cuántos puntos (vértices) formas ese contorno, permitiendo reconocer formas. Tras varias pruebas con distintas formas (triángulos, cuadrados, rectángulos, pentágonos y círculos) y varias iluminaciones y puntos de vista, concluí que el triángulo era la que aportaba más robustez

## 6. Otras opciones para el procesado de imagen

Para procesar la imagen, tal y como mencioné anteriormente, me baso en una segmentación que dejen sólo las zonas verdes en blanco y lo demás negro. De esta forma, de esa nueva imagen, puedo buscar contornos, discriminarlos por forma y tamaño y, finalmente calcular el centroide del triángulo verde más grande, obteniendo el centro aproximado del identificador.
En ocasiones hay algo de ruido, ya que por reflejos o simplemente porque hay colores cercanos al buscado, aparecen pequeñas zonas blancas no deseadas. En el caso del identificador de 4 puntos con 4 colores, al haber tantos colores, había más ruido, por lo que me veía obligado a aplicar una erosión para suprimir ese ruido, evitando detecciones erróneas pero también aumentando más la carga computacional. En

24 el caso del identificador que escogí como definitivo (un único triángulo verde), este problema no tenía importancia porque las discriminaciones acababan con el ruido y la aproximación del algoritmo de clasificación de formas elimina irregularidades en los bordes.
Es importante que, con tal de incrementar muy notablemente la robustez, la umbralización la hago en el espacio de color HSV en lugar de en el RGB que percibe la cámara. A pesar de que realizar esta conversión previa es la tarea que más tiempo consume en todo el proceso, segmentar en RGB daba unos resultados completamente inaceptables. Esto es por la forma de codificar la información, ya que, a diferencia de RGB, HSV separa la información de intensidad de luz de la del tono del color, siendo muchísimo más robusto a cambios de iluminación. A pesar de que esto también se estructura así en otros espacios de color, HSV es ampliamente utilizado en la visión por computador, así que en la mayoría de librerías para este ámbito, las transformaciones entre RGB y HSV están muy pulidas. Por otra parte, en HSV los colores se representan en un cilindro, no en un cubo, como en RGB, lo que hace bastante más sencillo establecer los márgenes inferior y superior de los umbrales.

## 7. Otras opciones para las comunicaciones

En un principio utilizaba comunicación TCP tanto para leer la posición de la herramienta respecto a la base como para ordenar los movimientos (mi programa aplicaba las correcciones a la posición de cada instante y ordenaba los desplazamientos o velocidades deseados). Sin embargo, luego me di cuenta de que esto era eficientemente mejorable enviando únicamente las correcciones al robot y que él se encargue de aplicarlas a su posición y de moverse, haciendo que el UR se cargue con esas operaciones mientras la Raspberry sigue con la siguiente captura de imagen y su procesado. Para esto escribía cuatro registros a través de Modbus TCP, dos con las correcciones cartesianas (en milímetros, ya que sólo se pueden almacenar enteros) a hacer por el robot y otros dos con los signos de dichas correcciones (0 si era en el sentido negativo del eje y 1 si era en el positivo), ya que sólo se permiten números positivos en los registros. De este modo, pasé de tener que leer 17 paquetes TCP sólo para saber la herramienta (lo leía desde el programa del robot con get actual tcp pose() directamente) y también, aunque tenga menos repercusión, me ahorraba la creación, e inicialización de varias variables, acceder a sus posiciones de memoria, sumarle el contenido de las correcciones, hacer casts a strings para enviar el comando, etc.
Es importante puntualizar que esto no sirve para el programa que usa control visual clásico, ya que ese obtenía las velocidades articulares, así que lo más óptimo que se me ocurrió fue pasar directamente el comando, ya que si no tendría que escribir 12 registros (6 velocidades y 6 signos) y desde el programa del robot leerlos todos, hacer

25 comparaciones, modificar variables, etc. Además, tal y como implementé ese programa, no requiere la intervención de ningún programa del robot, bastaba con conectar la Raspberry al armario pero funcionaba peor que el definitivo.

## 8. Análisis de resultados y conclusiones

Con tal de analizar los resultados que he obtenido (y discriminar o tomar algunas mejoras), medí los tiempos para comprobar cómo de útil sería modificar ciertas partes de mi algoritmo. Para obtener medidas lo más reales posibles, tomé cinco iteraciones distintas del bucle principal del algoritmo de programación, todas ellas noconsecutivas y analicé teniendo en cuenta la media y la disparidad de estos resultados. Las medidas que obtuve fueron:

Proceso | Medida 1 | Medida 2 | Medida 3 | Medida 4 | Medida 5 | Media
Caputra de imagen | 0.00433 | 0.00439 | 0.00493 | 0.00459 | 0.00461 | 0.00457
Conversión RGB-HSV | 0.01514 | 0.01584 | 0.01526 | 0.01539 | 0.01482 | 0.01529
Segmentación | 0.00923 | 0.02191 | 0.00941 | 0.00917 | 0.00871 | 0.011686
Búsqueda contornos | 0.00397 | 0.004 | 0.00413 | 0.00418 | 0.00364 | 0.003984
Búsqueda área máxima | 0.0002 | 0.00017 | 0.0001 | 0.00011 | 0.00013 | 0.000142
Cálculo centroide | 0.00018 | 0.00018 | 0.0001 | 0.00014 | 0.00014 | 0.000148
Media móvil | 0.00008 | 0.00005 | 0.0001 | 0.00006 | 0.00007 | 0.000072
Cálculo de correcciones | 0.00004 | 0.00003 | 0.00003 | 0.00005 | 0.00005 | 0.00004
Escritura Modbus | 0.00540 | 0.00704 | 0.00637 | 0.0099 | 0.00674 | 0.00709

Cuadro 1: Mediciones de tiempos de proceso (en segundos)

Salvo en algún caso puntual, como en la segmentación, que en la segunda medida da un tiempo de 20ms cuando evidentemente la tendencia ronda los 10 ms, en todos los casos se observa una tendencia bastante clara en cuanto a consumo temporal, por lo que puedo confirmar que fueron unas pruebas válidas.
De estas medidas puedo extraer dos lecturas importantes:

El tiempo aproximado de una iteración completa del bucle, que resultará de sumar todoas las medias, es decir: (0.04583 + 0.0502 + 0.04718 + 0.04962 + 0.04965)/5 = 0.048496 s. Redondeando, estimo que en cada iteración se invierten 50 milisegundos, por lo que al robot se le envían correcciones con esa cadencia, siendo aproximadamente 5 veces la máxima velocidad a la que pueden enviársele órdenes (8 ms)

El procesado visual es lo que más tiempo consume. Con un total de 0.031244

26

(aproximadamente 30 ms), en el procesado visual se invierte sobre un 70 % del total del tiempo invertido en cada bucle, por lo que éste debe de ser el principal objetivo en las optimizaciones futuras que vayan a hacerse

Tras el trabajo realizado así como los resultados obtenidos, concluyo que creo que si se siguiese desarrollando esta aplicación, podría llegarse a algo realmente práctico y útil en el mundo industrial. Tal y como mencioné en la introducción, considero que con un sistema de este tipo se logra mejorar sustancialmente la comodidad y facilidad de programación, ya que el usuario tan sólo tendrá que realizar la tarea con normalidad, con la única diferencia de colocar una pegatina en su herramienta o, en el peor de los casos, añadirle una pequeña placa donde pueda colocársele dicho identificador.
Por otro lado, a título personal, estas prácticas me han servido para desarrollarme tanto desde un punto de vista personal como desde un enfoque técnico. En este último aspecto he adquirido experiencia con los robots de Universal Robots así como mucha más soltura con Python. También he aprendido bastante sobre redes y comunicaciones de una forma más transversal. Considero que he mejorado mi capacidad de análisis de resultados y de organización, tanto de mi tiempo como en el desarrollo de software y de piezas 3D. En lo personal, he conocido puntos de vista de gente con experiencia laboral fuera del ámbito académico y he acumulado una gran cantidad de vivencias que me han motivado aún más a seguir formándome e incluso me han inspirado para volver a sentirme atraido por campos por los que había disminuido mi interés.

## 9. Trabajos futuros

Tal y como mencioné en la introducción, este proyecto no tenía el objetivo de lograr una implementación totalmente refinada lista para lanzarse al mercado, sino iniciar una posible vía hacia dicha funcionalidad. Por esto, me pareció de gran relevancia mencionar algunos de los trabajos futuros que podrían realizarse para avanzar a partir del punto al que he llegado.

9.1. Optimización

Una de las maneras más inmediatas de lograr acelerar el procesado desde la Raspberry es deshabilitar servicios inútiles que estén ejecutándose en la misma. Este dispositivo es un ordenador y, como tal, la ejecución del programa de esta aplicación no es su prioridad y está ejecutando una gran cantidad de subprocesos que limitan el tiempo durante el que mi programa tiene disponible los recursos de computación.
Otro avance en cierta medida relacionado con el anterior sería implementarlo todo en una FPGA para, posteriormente, crear un ASIC que realice todo el proceso o, al menos, el procesado de la imagen (que es lo más pesado) de la forma más rápida

27 posible. En este tema hay que tener varios aspectos en cuenta. El principal es la cámara, ya que su velocidad de captura y la forma que tenga de enviar los datos que capte casi con total seguirdad pasarán a ser el cuello de botella de la aplicación. Podría reducirse el impacto de esto de una forma tan sencilla como utilizando la cámara del mercado que mejor se adapte a las necesidades como de una tan compleja como diseñando una cámara con una interfaz de comunicación especial para esta aplicación.
Por último, hay ciertas partes del código que pueden ser paralelizadas, tanto del procesado de la imagen (como la umbralización) como de algunas otras operaciones, en las que habría que evaluar hasta qué punto es práctico tener que abrir y cerrar un hilo de ejecución únicamente para realizarlas, aunque puede que sea útil mantenerlo activo hasta que se acabe el programa haciendo que los hilos sean bucles infinitos y sincronizándolos con el programa con mutex o cualquier otra técnica que se ajuste lo mejor posible a nuestros requerimientos.
Dada la menor exigencia de recursos durante la reproducción de movimientos, podría instalarse otro controlador menos potente que el principal que se encargue de llevar a cabo esta tarea, permitiendo así reducir el consumo, aunque seguramente sea una reducción despreciable dado el elevado consumo que implicará el uso del robot.
9.2. Mejoras de funcionalidades

A pesar de que ya de por sí la funcionalidad de mejorar la programación por guiado tradicional puede ser suficiente, esta puede verse afectada por algunos factores que podrían empeorar o, en casos extremos, llegar a inutilizarla. Por esto y, dado que se usa visión artificial, crear una interfaz que permita calibrar los umbrales y algunas partes del proceso de forma sencilla puede ser una mejora muy práctica, así como bastante sencilla de implementar.
Por otra parte, a costa de aumentar ligeramente la voluminosidad del soporte, incluir una batería o hacer que reciba energía del conector de herramientas del robot sería muy práctico, ya que supondría poder prescindir de uno de los dos cables que requiere la herramienta. Para esta última opción, podría transformarse una de las salidas a 12 voltios del conector a los 5 que requiere la Raspberry.
Siguiendo con la intención de reducir el cableado, si se desarrollase una interfaz wifi para el UR podría lograrse una aún mayor simpleza en este aspecto, logrando eliminar todos los cables que se exigen para la aplicación. El principal problema de esto reside en la seguridad, que se ve vulnerada por las comuniciones inalámbricas. Por esto, otra buena opción podría se desarrollar una comunicación a través del conector de herramienta o investigar otras opciones inalámbricas más seguras que el Wi-Fi convencional. Una opción muy factible y más aún si se alimenta a la Raspberry desde el conector de herramienta sería utilizar las comunicaciones que incorporan los nuevos robots e-series para realizar la escritura de los registros Modbus, pudiendo eliminar todos los cables de la herramienta.

28

9.3. Otras mejoras

Dada la simplificación que realicé pasando del control visual clásico a uno mucho más simple, este método sólo puede utilizarse para programar actividades que se realicen sobre superficies más o menos planas, ya que el robot desplazará su extremo en el plano donde se encontrase inicialmente. Una opción para mejorar esto podrìa ser combinar la visión artificial con odometría más convencional, como podría ser un giroscopio (a ser posible, combinado con un acelerómetro para poder hacer uso de un filtro que combine ambas medidas, estabilizando mucho más las lecturas).
También podría realizarse un control más avanzado, aunque seguramente suponga un aumento del coste computacional. Quizás incluir realimentaciones o partes integral o derivativa mejoren el comportamiento. En favor de la robustez, considero que se debería priorizar la estabiliidad. Dado que el robot ya corrige muy bien la forma de alcanzar las posiciones, haciendo el control de verdad por sí mismo, comenzaría centrándome en estabilizar las conclusiones a las que el algorimto lleva, es decir, lograr hacer que las correcciones que se envían por Modbus sean todo lo estables posibles permitiendo un tracking lo más veloz posible.
Otra posible mejora sería el desarrollo de un URCap que permita que el programa del robot sea más estético y pueda ser más sencillo utilizarlo para otras aplicaciones más complejas en las que pueda ser útil este desarrollo.
Por último, para una aplicación industrial real, la herramienta que he diseñado no es válida, ya que no garantiza protecciones demasiado relevantes, por lo que habría que contemplar el uso de otros materiales, opciones para sellarla, quizás incluir LEDs de estado que indiquen el correcto funcionamiento de cada componente (ventilación, sensores, comunicaciones, etc.).

29

## Referencias

[1] Especificaciones | del | modulo | de | c ´ | amara: ´
https://elinux.org/Rpi Camera Module#Technical Parameters .28v.2 board.29
[2] Lectura | del | sensor | de | distancia | HC-SR04:
https://robologs.net/2015/07/31/tutorial-de-raspberry-pi-y-hc-sr04/
[3] Documentacion de OpenCV: ´ | https://opencv.org/releases.html
[4] Documentacion | de | pymodbus | (para | clientes | s ´ | íncronos):
https://pythonhosted.org/pymodbus/library/sync-client.html
[5] Herramienta on-line para diagramas: https://www.lucidchart.com/
[6] Herramienta para diseno 3D: ˜ | https://www.freecadweb.org/
[7] Tutoriales | oficiales | de | Universal | Robots: | https://www.universal-
robots.com/how-tos-and-faqs/how-to/
[8] Zacobria (foro de consulta sobre robots UR): http://www.zacobria.com/
[9] Robotiq (foro de consulta de robotica): ´ | https://robotiq.com/
[10] Lectura | de | la | IMU MPU6050 (la | utilice | para | algunas | pruebas): ´
http://blog.bitify.co.uk/2013/11/reading-data-from-mpu-6050-on-raspberry.html

30

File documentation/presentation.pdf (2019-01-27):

Motivación y objetivos
Resultados
Análisis de resultados
Alternativas

# Propuesta de un método alternativo de programación por guiado basado en visión artificial


### I Concurso de Aplicaciones Robóticas CFZ Cobots

# Diciembre de 2018

TORRES CAMARA, José Miguel ´ | Propuesta de un método alternativo de programación por guiado | basado en visión artificial

Alternativas

1 | Motivación y objetivos Introducción Objetivos
2 | Resultados Herramienta desarrollada Script de programación Script de reproducción Programa del robot
3 | Análisis de resultados
4 | Alternativas

Alternativas

Introducción
Objetivos

# Índice

1 | Motivación y objetivos Introducción Objetivos
2 | Resultados Herramienta desarrollada Script de programación Script de reproducción Programa del robot
3 | Análisis de resultados
4 | Alternativas

Alternativas

Introducción
Objetivos

# Índice

1 | Motivación y objetivos Introducción Objetivos
2 | Resultados Herramienta desarrollada Script de programación Script de reproducción Programa del robot
3 | Análisis de resultados
4 | Alternativas

Alternativas

Introducción
Objetivos

# Tipos de programación

# Textual Por guiado

## Discreta: Mover el robot hasta puntos, almacenarlos y usarlos en un programa Directa: Realizar tarea con herramienta anclada

Alternativas

Introducción
Objetivos

# Programación por guiado directa

# Ventajas:

## Conservar el arte del operario Sencillez

# Desventajas:

## Imprecisión Incomodidad Limitaciones Esfuerzo extra

Alternativas

Introducción
Objetivos

# Índice

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

Alternativas

Introducción
Objetivos

# Objetivos

# Mantener ventajas y reducir desventajas

# Propuesta, NO alternativa real Prototipo mínimo que permita:

## Demostrar posibilidad de implementación Proponer un punto de partida Descubrir errores y mejoras

Alternativas

Introducción
Objetivos

# Target

# Herramienta plug & play

# Tracking de identificador (invariante a dimensiones, relaciones e iluminación)

# Almacenar correcciones relativas

# Reproducir correcciones

Robusto → Cambios de iluminación, entornos diferentes, etc. Efectivo → Seguimiento, velocidad, suavidad, precisión, etc.

# Sencillo → user-friendliness y plug & play

# Práctico → Embedido, pequeño y manejable

Alternativas

Herramienta desarrollada
Script de programación
Script de reproducción
Programa del robot

# Índice

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

Alternativas

Programa del robot

# Índice

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

Alternativas

Programa del robot

# Modelo 3D


Alternativas

Programa del robot

# Otras opciones

# Primer anclaje → Bridas y cinta adhesiva

# Segundo anclaje → Placas paralelas

# Otros diseños → Adaptar carcasas de RPi y soportes para cámara

Alternativas

Programa del robot

# Segundo anclaje


Alternativas

Programa del robot

# Versión definitiva


Alternativas

Programa del robot

# Versión definitiva


Alternativas

Programa del robot

# Índice

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

# Diagrama de flujo


Alternativas

Programa del robot

Alternativas

Programa del robot

# Bucle principal: Procesado de imagen

# Umbralización


Alternativas

Programa del robot

# Bucle principal: Procesado de imagen

# Extracción de contornos


Alternativas

Programa del robot

# Bucle principal: Procesado de imagen

# Doble discriminación


# Bucle principal: Procesado de imagen


Alternativas

Programa del robot

Alternativas

Programa del robot

# Bucle principal: Cálculo de correcciones


Alternativas

Programa del robot

# Bucle principal: Cálculo de correcciones


Alternativas

Programa del robot

# Bucle principal: Procesado de correcciones

# Escribir correcciones en registros Modbus-TCP

## 128 y 129 para datos 130 y 131 para signos (”1” para positivos y ”0” para negativos)

# Dividir corrección por 2 (reduce velocidad y oscilación)

# Escribir en el logfile

Alternativas

Programa del robot

# Proceso de finalización

# Poner a 0 los registros

# Liberar cámara

# Cerrar socket

# Liberar archivo de historial

# Reset de GPIOs

Alternativas

Programa del robot

# Índice

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

# Diagrama de flujo


Alternativas

Programa del robot

Alternativas

Programa del robot

# Índice

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

Alternativas

Programa del robot

# Diagrama de flujo


Alternativas

# Índice

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

Alternativas

# Consumo temporal (s)

Proceso | Medida 1 | Medida 2 | Medida 3 | Medida 4 | Medida 5 | Media
Caputra de imagen | 0.00433 | 0.00439 | 0.00493 | 0.00459 | 0.00461 | 0.00457
Conversión RGB-HSV | 0.01514 | 0.01584 | 0.01526 | 0.01539 | 0.01482 | 0.01529
Segmentación | 0.00923 | 0.02191 | 0.00941 | 0.00917 | 0.00871 | 0.011686
Búsqueda contornos | 0.00397 | 0.004 | 0.00413 | 0.00418 | 0.00364 | 0.003984
Búsqueda área máxima | 0.0002 | 0.00017 | 0.0001 | 0.00011 | 0.00013 | 0.000142
Cálculo centroide | 0.00018 | 0.00018 | 0.0001 | 0.00014 | 0.00014 | 0.000148
Media móvil | 0.00008 | 0.00005 | 0.0001 | 0.00006 | 0.00007 | 0.000072
Cálculo de correcciones | 0.00004 | 0.00003 | 0.00003 | 0.00005 | 0.00005 | 0.00004
Escritura Modbus | 0.00540 | 0.00704 | 0.00637 | 0.0099 | 0.00674 | 0.00709

Alternativas

# Consumo temporal

# Tiempo medio: 0.048496 s (5x vel. máxima de envío de órdenes del robot)

# Mayor gasto: Procesado visual (0.0312 s, 70% del total)

⇓

# Optimizar procesado de imagen

Alternativas

# Índice

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

Alternativas

# Alternativas

# Herramientas

# Identificadores

# Procesado de imagen

# Control/cálculo de correcciones

# Comunicaciones

# Adquisición de datos

Alternativas

# Gracias por vuestra atención


# CFZ Cobots

# I Concurso de Aplicaciones Robóticas

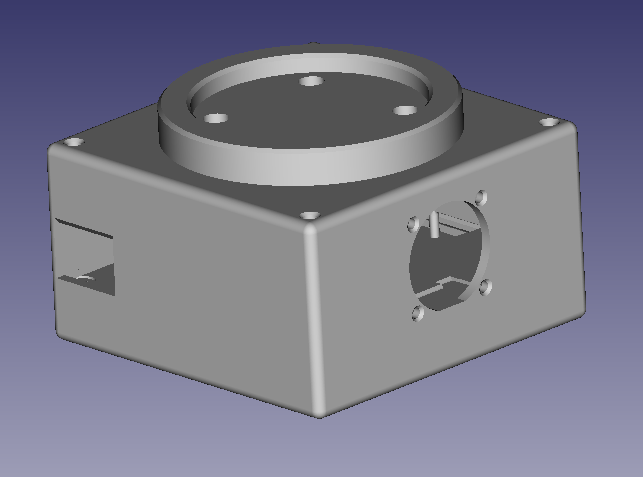
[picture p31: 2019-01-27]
multimedia/3d_case/full_upView.png

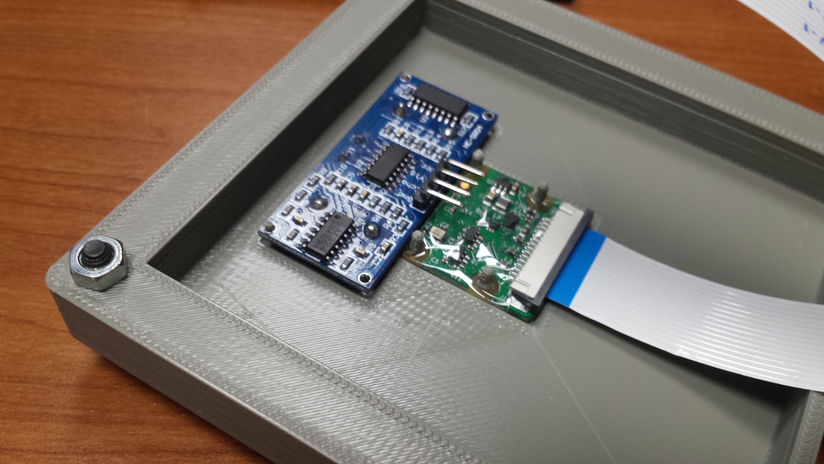
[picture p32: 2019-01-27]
multimedia/3d_case/real_bottomPlate_sensorAndCamera.jpg

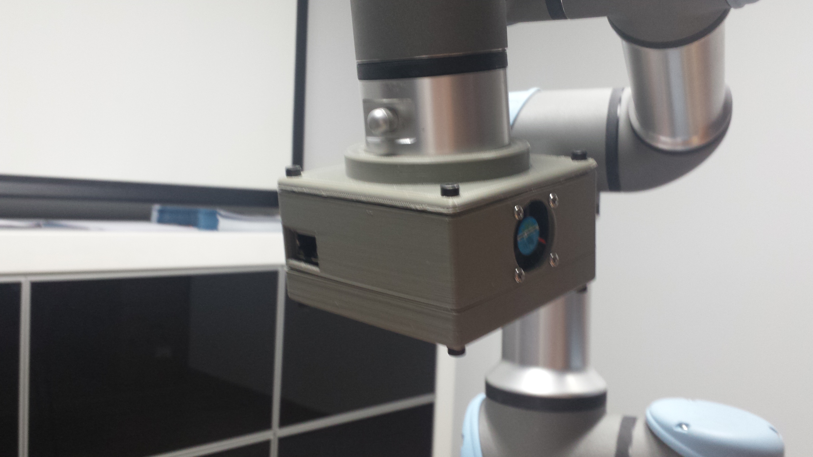
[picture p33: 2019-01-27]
multimedia/3d_case/real_full_upView.jpg

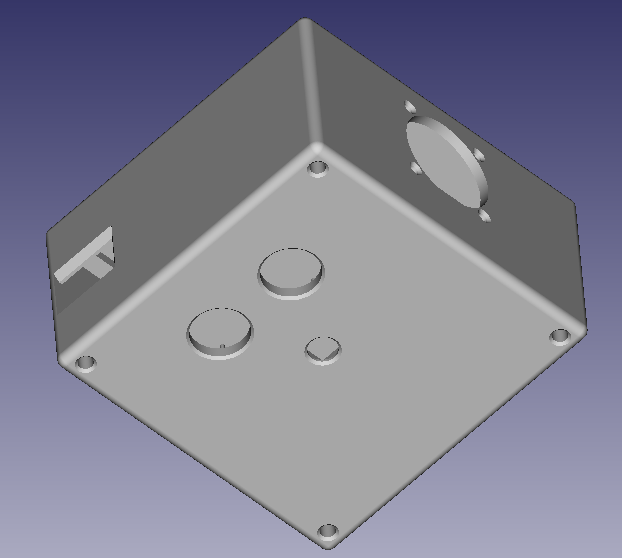
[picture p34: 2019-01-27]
multimedia/3d_case/full_downView.png

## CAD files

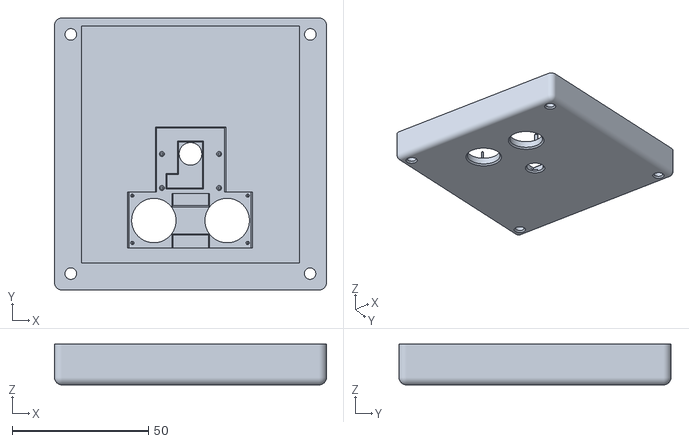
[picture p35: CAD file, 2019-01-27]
3d_case/pieces_in_stl/placaInferior.stl
100.0 x 100.0 x 15.0

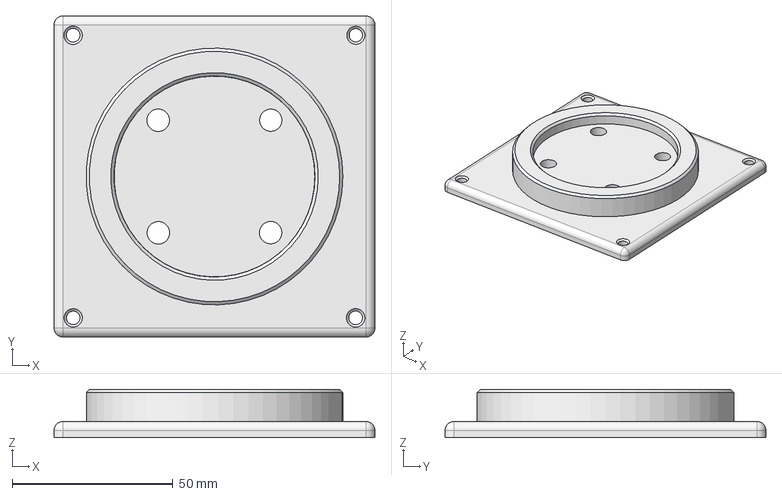
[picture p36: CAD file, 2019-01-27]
3d_case/placaSuperior_v2.fcstd
100.0 x 100.0 x 15.0 mm

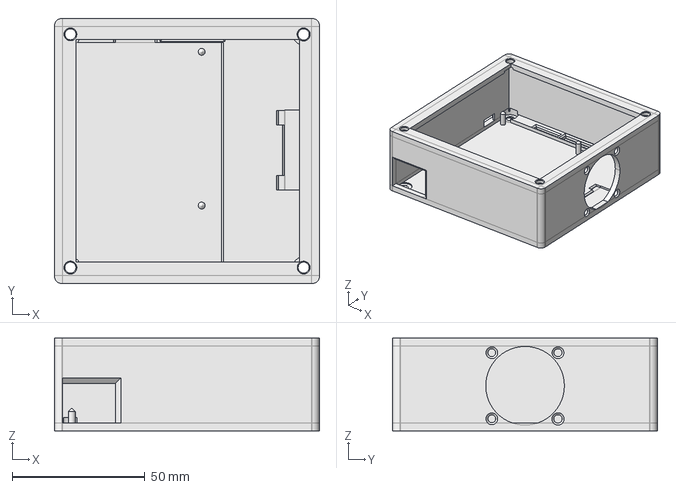
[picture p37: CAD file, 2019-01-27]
3d_case/placaMedia_v2.fcstd
100.0 x 100.0 x 35.0 mm

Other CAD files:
3d_case/pieces_in_stl/placaSuperior.stl
3d_case/pieces_in_stl/placaMedia.stl
3d_case/placaInferior_v2.fcstd

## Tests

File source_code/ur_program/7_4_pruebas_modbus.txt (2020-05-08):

 Programa
   Programa de robot
     'MoveJ'
     pose_tcp≔get_actual_tcp_pose()
     corrX≔read_port_register(128)
     corrY≔read_port_register(129)
     pose_corregida≔pose_trans(pose_tcp, p[corrX/1000,corrY/1000,0,0,0,0])
     If corrX≠0 or corrY≠0
       If read_port_register(130)≟0
         corrX≔-corrX
       If read_port_register(131)≟0
         corrY≔-corrY
       MoveL
         pose_corregida
     Esperar: 0.01

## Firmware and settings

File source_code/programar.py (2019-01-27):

print("\n\n[<]Iniciada programacion por vision artificial[>]\n\n")
print("[#]Iniciado proceso de configuracion previa")


###### ### ##  IMPORTACION DE DEPENDENCIAS  ## ### ######



print("    [*]Importando dependencias...")

#Para uso general
import time #Para contar tiempo (time()) y hacer pausas (sleep())

#Para el tracking
import numpy as np
import cv2

#Para escribir por MODBUS TCP
from pymodbus.client.sync import ModbusTcpClient as ModbusClient
from pymodbus.client.sync import ModbusTcpClient as ModbusClient

#Para saber si un archivo existe
import os.path

#Para leer del HC-SR04
import RPi.GPIO as GPIO






###### ### ##  C O N S T A N T E S   D E   C O N F I G U R A C I O N  ## ### ######



print("    [*]Realizando configuraciones generales...")

#Comunicaciones
HOST = "192.168.1.147" #IP del robot
PORT_MODBUS= 502 #Puerto donde el robot tiene el servidor (esclavo) Modbus

#Constantes para el sensor
CORRECCION_SENSOR = -0.006 #Distancia entre el sensor y la camara en Z en metros (para corregir la lectura)
DISTANCIA_CAMARA_PAPEL = 0.2715 #Distancia camara-superficie

#Longitud del filtro de media movil -> A mas longitud -> Mas precision y menos velocidad
LONG_FILTRO = 4 

#Umbrales de area para considerar valida una deteccion de caracteristica
AREA_LOW = 500 #Estaba a 200
AREA_TOP = 6500 #Estaba a 15000

#Zona donde se considera que la camara esta sobre el centro (Valor de menos a mas estricto: 10-30)
ZONA_TOLERANCIA = 14






###### ### ##  F U N C I O N E S   A U X I L I A R E S  ## ### ######



#Funcion para hacer la media movil (recibe los historiales de posiciones del identificador)
def media_movil(historial_cx, historial_cy):
	sumax = 0
	sumay = 0
	contador = 0
	
	#Recorrer los historiales de valores y  sumar los elementos
	while contador < LONG_FILTRO:
		sumax += historial_cx[contador]
		sumay += historial_cy[contador]

		contador += 1
	
	return sumax/LONG_FILTRO, sumay/LONG_FILTRO #Devolver la media



#Funcion para clasificar formas (recibe un contorno)
def detectarTriangulo(c):
	#Aproximar el contorno con lineas rectas 
	peri = cv2.arcLength(c, True)
	approx = cv2.approxPolyDP(c, 0.04 * peri, True)

	#Si la aproximacion se ha resuelto con tres puntos (vertices)
	if len(approx) == 3:
		return True #Confirmar que la forma es un triangulo
	else:
		return False
		
		
		
#Funcion para medir distancia con el HC-SR04 (asume que Trig y Echo se han inicializado antes de la llamada con los pines donde este conectado el sensor)
def medirDistancia():
	GPIO.output(Trig, False) #Apagar el pin Trig (disparador)
	time.sleep(2*10**-6) #esperar 2 us
	GPIO.output(Trig, True) #Encender Trig 
	time.sleep(10*10**-6) #esperamos 10 us
	GPIO.output(Trig, False) #Apagar Trig
 
	#Empezar a contar el tiempo cuando el pin Echo se encienda
	while GPIO.input(Echo) == 0:
		start = time.time()
 
	while GPIO.input(Echo) == 1:
		end = time.time()
 
	#Calcular tiempo transcurrido entre inicio y fin (en segundos) 
	duracion = end-start

	#Pasar tiempo a microsegundos
	duracion = duracion*10**6
	medida = duracion/58 #Calcular distancia en cm
	medida = medida/100 #Pasar medida a metros

	return medida #Devolver distancia recibida






###### ### ##  O T R A S   I N I C I A L I Z A C I O N E S  ## ### ######



#Inicializar camara
print("    [*]Accediendo a la camara...")
cap = cv2.VideoCapture(0)
ret, frame = cap.read()

if(ret == False):
	print("    [!]ERROR! Ha sido imposible acceder a la camara")
	
	
#Inicializaciones para el sensor
print("    [*]Preparando modulo HC-SR04...")
GPIO.setwarnings(False) #Ignorar posibles fallos en otros programas que no limpiasen los puertos
GPIO.setmode(GPIO.BOARD) #Usar la numeracion de la placa
#Definir los pines donde se conectaran Trigger y Echo
Trig = 11
Echo = 13
#Configurar ambos pines 
GPIO.setup(Trig, GPIO.OUT)
GPIO.setup(Echo, GPIO.IN)


#Inicializar comunicaciones
print("    [*]Configurando comunicaciones...")
client = ModbusClient(HOST, PORT_MODBUS) #Abrir puerto de comunicacion con el robot (para enviar valores por MODBUS)
comunicacion_OK = True

if(client.connect() == False):
	print("    [!]ERROR! Ha sido imposible conectarse al servidor Modbus")
	comunicacion_OK = False
	ret = False


#Abrir archivo de escritura
print("    [*]Abriendo archivo para almacenar los movimientos...")
respuesta = "s"
if(os.path.isfile("./correcciones.txt")): #Si ya existe el archivo en el directorio desde el que se ejecuta el programa
	while(1):
		respuesta = raw_input("    [!]ALERTA! Existe un 'correcciones.txt' en el directorio actual. Desea continuar (y sobreescribirlo)? (s/n): ") #Pedir autorizacion para seguir (y sobreescribirlo)
		
		if(respuesta == "n"): #Si NO se quiere
			ret = False #Acabar programa
			break
		elif(respuesta == "s"): #Si SI se quiere
			archivo = open("correcciones.txt", "w") #Abrir archivo
			break
		else: #Si se introduce una respuesta no valida
			print("    [!]ERROR! No se ha introducido una respuesta valida. Introduzca 's' para seguir adelante o 'n' para abortar la ejecucion")
else:
	archivo = open("correcciones.txt", "w")
		
		
#Variables para el procesado de imagen
print("    [*]Preparando el procesado de imagen...")
err_areaNoDetectada = False
#Rango de color a coger
verde_min = (40, 30, 40)
verde_max = (60, 215, 215)
#Leer tamano de la imagen
w = cap.get(3)
h = cap.get(4)
#Inicializar variables del centro, area y contorno (para evitar inicializaciones y destrucciones en bucle)
cx = w/2
cy = h/2
area = 0.0
area_max = 0.0
it = 0


#Inicializaciones para el control (variables y ajuste de distancia camara-superficie)
print("    [*]Adaptando el algoritmo al entorno...")
#Variables para el control
correccionX = 0
correccionY = 0
cambioX = False
cambioY = False
historial_x = []
historial_y = []
#Actualizar las correcciones maximas que se haran
contador = 0

#Medir LONG_FILTRO*2 veces la distancia y hacer la media
while(contador<LONG_FILTRO*2):
	DISTANCIA_CAMARA_PAPEL += medirDistancia() #Tomar medida del sensor
	contador += 1
DISTANCIA_CAMARA_PAPEL = DISTANCIA_CAMARA_PAPEL/LONG_FILTRO + CORRECCION_SENSOR #Calcular media de medidas y restar 5 cm para conseguir variaciones mas pequenyas
#Actualizar desplazamientos partiendo de la altura de la camara
DESPLAZAMIENTO_MAX_X = 0.6032385667*DISTANCIA_CAMARA_PAPEL
DESPLAZAMIENTO_MAX_Y = 0.4507693885*DISTANCIA_CAMARA_PAPEL



#Si NO se ha indicado ningun error
if(ret == True):
	#Informar del inicio del proceso principal
	print("\n[#]Todo listo! Iniciado bucle de control principal")
	print("    [!]AVISO: Recuerde iniciar la ejecucion del programa del robot")
	raw_input("    [*]Pulse 'Enter' para continuar...")
	print("\n")






###### ###### ### ## #   ###### ### ##  #  ## ### ######   # ## ### ######

###### ### ##  I N I C I O   D E   B U C L E   P R I N C I P A L  ## ### ######

###### ###### ### ## #   ###### ### ##  #  ## ### ######   # ## ### ######
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

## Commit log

2019-01-27 Upload source codes
    The "programar.py" file, which makes the robot follow the biggest green triangle and store the trajectory it is following in a file.
    The "reproducir.py" script reads the file created by "programar.py" and makes the robot follow the trajectory in it (starting from whichever the pose it currently is at).
2019-01-27 Create "3d_case" directory
    Here I will upload the 3D files to print the final version of the case
2019-01-27 Upload the ".fcstd" files
    The 3D models of the three plates in .fcstd format: the bottom (placaInferior), middle (placaMedia) and upper (placaSuperior) plates.
    [placaInferior_v2.fcstd, placaMedia_v2.fcstd, placaSuperior_v2.fcstd]
2019-01-27 Upload "gcode" files, ready to print
    Upload the files of the three plates (bottom, middle and upper) ready to 3D-print, in .gcode files.
2019-01-27 Upload ".stl" files, more standard
    Upload the plates (bottom, middle and upper) in .stl format, a way more standard filetype than .fcstd
    [placaInferior.stl, placaMedia.stl, placaSuperior.stl]
2019-01-27 Create a
    Create "multimedia" directory to upload relevant videos and pictures.
    Create "multimedia/3d_case" directory to upload pictures of the 3D model and printed case
2019-01-27 Upload 3D-printable case pictures
    Upload pictures of the 3D case. Some of the real printed pieces (the ones which names starts with "real_...") and some screenshots of the 3D model in the PC.
2019-01-27 Create "demo_videos" directory and upload shape and color recognition
    Upload a shape and color recognition demo. This process is included in the working flow of the source file "programar.py".
2019-01-27 Upload v1 case pictures
2019-01-27 Update README.md
    Added introduction and start the 3D case section
2019-01-27 Added "scripts" section
    Added the "scripts" section, explaining their working flow
2019-01-27 Upload final behaviour demo
    In this video, I make a square trajectory with the identifier and the robot tracks and store it. Finally, the arm reproduces it.
2020-05-08 Add demo GIFs to README
    These GIFs will be used in the README to illustrate a part of the process and sample achieved results. They also serve as the link to the YouTube videos with the full demos.
